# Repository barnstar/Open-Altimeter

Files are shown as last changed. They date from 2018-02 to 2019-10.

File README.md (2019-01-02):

# OpenAltimeter

## Concept

This was originally a project to build a simple altimeter to record
the apogee of mid power rocket flights... Then things got out of hand
as they are liable to do in this hobby........

The complex version runs on  an ESP8266 (or compatible) and includes 
sensor fusion to calculate spatial orientation, pyro and servo channels,
a web server and an  oled display to provide a "nice" user interface.

The "simple" version is designed for an Arduino nano and has no
interface beyond the serial logger and the indicator LEDs.

## Hardware

To build this, you'll need an Arduino - a nano is best or an ESP8266.
An ESP12 should also work but hasn't been tested.

The pinouts are noted in Configuration.h.  There are several
LEDs for indicators, a pin for an active peizo and two pins which
can be used for firing ematches via an NPN mosfet.  Two pins are also
allocated to control servos for parachute deployment (and/or for active
flight control for the ambitious).

The complex version also includes support for Oled displays via i2c.
A second switch can be used to navigate between the screens.

Notes:
- Power can be supplied from a 2s lipo.  Both the arduino nano
  and ESP8266 based boards like the Node MCU v1.0 will happily run off
  of an ~7.4V supply.   If using a nano with only a barometer, you
  can also use a pair of lithium button cells to construct a unit not 
  much larger than a a commercial altimeter.
- For deployment, it is advised to add a ~1A 5V regulator to drive
  the servos and/or mosfets.  You can get away with powering a small
  piezo and the indicator LEDs directly from the logic pin but be
  cautious.  Use a transistor switch for anything that exceeds the 
  single pin current rating for whichever micro controller you choose.
  You may be able to drive a small servo from the arduino 5V Vout as
  well.  This will not work for any board with 3.3V logic.

...Happy Flying

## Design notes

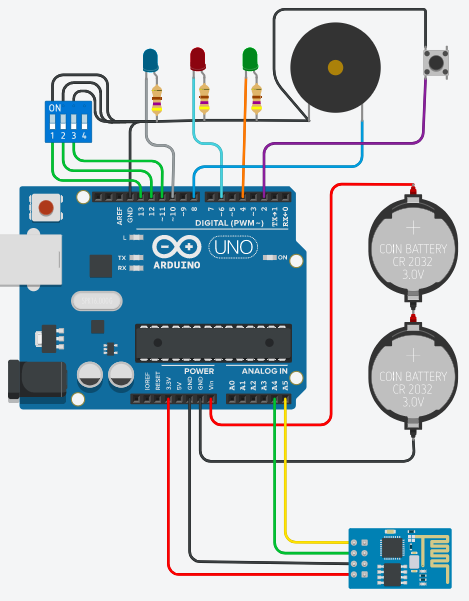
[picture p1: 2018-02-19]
Schematic.png

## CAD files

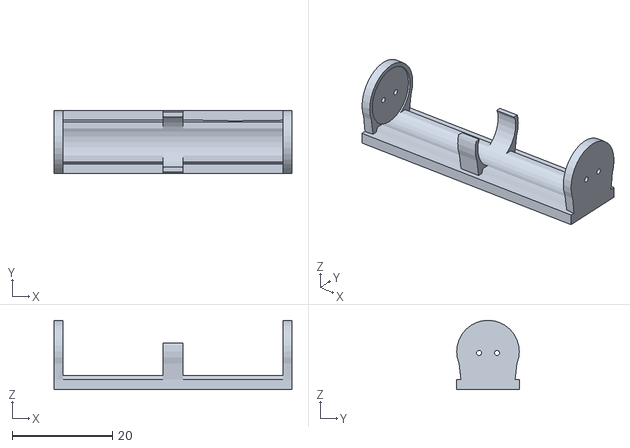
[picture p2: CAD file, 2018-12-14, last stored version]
Mechanical Parts/AAA-single.stl
47.5 x 12.5 x 13.9

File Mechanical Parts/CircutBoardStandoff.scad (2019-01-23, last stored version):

// Prototype board standoffs
//
//  by Jonathan Nobels, 2019
//
//  I dedicate any and all copyright interest in this software to the public domain.
//  I make this dedication for the benefit of the public at large and to the
//  detriment of my heirs and successors. I intend this dedication to be an overt
//  act of relinquishment in perpetuity of all present and future rights to this
//  software under copyright law. See <http://unlicense.org> for more info.
//

//Large Proto Board
SO_W=46;
SO_L=66;

//Small Proto Board
//SO_W=16;
//SO_L=76;

//4 Relay Board
//SO_W=48;
//SO_L=69;

W = SO_W+8;
L = SO_L+8;
H = 2;

SO_OD = 7;
SO_ID = 2.4;
SO_H = 10;
CO_RATIO = .66;

$fn=60;

base();

translate([-SO_W/2, -SO_L/2,0]) 
standoff();

translate([SO_W/2, -SO_L/2,0]) 
standoff();

translate([-SO_W/2, SO_L/2,0]) 
standoff();

translate([SO_W/2, SO_L/2,0]) 
standoff();


module base() {
   {
    difference() {
      translate([-W/2, -L/2,0])
      cube([W,L,H]);
      cube([W*CO_RATIO,L*CO_RATIO,H*2],center=true);
    }
  }
}
  
module standoff()
{
  difference() {
   cylinder(r=SO_OD/2, h=SO_H); 
   cylinder(r=SO_ID/2, h=SO_H*2); 
  } 
}

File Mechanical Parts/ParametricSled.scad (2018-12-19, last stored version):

//Av bay inner tube diameter
AVBAY_ID = 66.6;

//Microcontroller standoff spacing
MC_SO_HSPACE = 12.5;
MC_SO_VSPACE = 22.5;

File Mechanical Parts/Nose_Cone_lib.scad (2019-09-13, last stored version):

// Parametric Nose Cones
// 2 or 3 piece with removable tip and sleeve
//
//  by Jonathan Nobels, 2017
//
//  I dedicate any and all copyright interest in this software to the public domain.
//  I make this dedication for the benefit of the public at large and to the
//  detriment of my heirs and successors. I intend this dedication to be an overt
//  act of relinquishment in perpetuity of all present and future rights to this
//  software under copyright law. See <http://unlicense.org> for more info.
//

//Cone styles
PARABOLIC = 1;
OGIVE = 2;
HAACK = 3;
ELLIPTICAL = 4;

STYLE = OGIVE;

$fn=50;

//Tube Sytles
TUBE_15MT = 0;   //1.5" Mailing Tube
TUBE_25MT = 1;   //2.5" Mailing Tube
TUBE_30MT = 2;   //3.0" Mailing Tube
TUBE_22TW = 3;   //2.2" Thick Wall (Rocketarium)
TUBE_25TW = 4;   //2.5" Thick Wall (Rocketaruim)
TUBE_BT80 = 5;   //Estes BT80 (2.5")
TUBE_BT60 = 6;   //Estes BT60
TUBE_BT50 = 7;   //Estes BT50
TUBE_BT55 = 8;   //Estes BT55

TUBE_TYPE = TUBE_22TW;


LENGTH  = 130;         //Overall length of nose cone
TIP_LEN = 20;         //Length of the removable tip
TIP_RAD = 2;          //Tip radius
SHOULDER_LENGTH = 67; //Length of the insert/avbay

//The radii and lengths here have to be customized for each length/od
//Deriving the raduis at a given z position is left as an exercise for
//the reader.
SLEEVE_OR = 22.5; //Tip insery sleeve outer radius
SLEEVE_IR = 11;   //Tip insert sleeve inner radius
SLEEVE_LEN = 15;  //Tip sleeve length

WALL_THICKNESS = 2.0; //Cone and sleeve wall thickness
TOL = 0.0;

SEGMENTS = 100;


DIAMETERS=[
    //1.5" Mailing Tube
    [38.2, 41.2],
    //2.5" Mailing Tube
    [63.65, 66.90],
    //3.0" Mailing Tube
    [75.75, 78.75],
    //Rocketarium thick wall 2.2" Tube
    //OD.: 2.26. I.D.: 2.14
    [2.14 * 25.4, 2.26 * 25.4],
    //Rocketarium thick wall 2.5" Tube
    //O.D.: 2.638. I.D.: 2.558
    [2.558 *25.4, 2.638 *25.4],
    //BT50 ID: 0.95", OD: 0.976"
    [0.95*25.4, 0.976*25.4],
    //BT60: ID: 1.595", OD: 1.637
    [1.595*25.4,1.637*25.4],
    //BT80: OD: 2.6" ID: 2.558"
    [2.558*25.4,  2.60*25.4],
    //BT55
    [32.6, 33.7]
];

TUBE_ID = DIAMETERS[TUBE_TYPE][0] - TOL;
TUBE_OD = DIAMETERS[TUBE_TYPE][1];


// Components
module bulkhead()
{
  difference()
  {
    union()
    {
      cylinder(r = TUBE_ID / 2, h = 3.5, center = false);
      cylinder(r = TUBE_ID / 2 - WALL_THICKNESS - .1, h = 6.0, center = false);
    }
    cylinder(r = 1.5, h = 20, center = true);
    for (x = [ -TUBE_ID / 2 + 8, TUBE_ID / 2 - 8 ])
    {
      translate([ x, 0, 0 ])
      {
        cylinder(r = 3.0, h = 20, center = true);
      }
    }
  }
}

module simple_insert_nobase()
{
  union()
  {
    difference()
    {
      union(){
      cylinder(r = TUBE_OD / 2 - WALL_THICKNESS, h = SHOULDER_LENGTH+10, center = false);
      cylinder(r = TUBE_ID / 2, h = SHOULDER_LENGTH, center = false);
      }
      translate([0,0,-3]) {
      cylinder(r = TUBE_ID / 2 - WALL_THICKNESS, h = (SHOULDER_LENGTH)*2.8, center = false);
      }
    }
  }
}

module simple_coupler()
{
  union()
  {
    difference()
    {
      union(){
      cylinder(r = TUBE_OD / 2 - WALL_THICKNESS, h = SHOULDER_LENGTH+10, center = false);
      cylinder(r = TUBE_ID / 2, h = SHOULDER_LENGTH, center = false);
      }
      translate([0,0,-3]) {
      cylinder(r = TUBE_ID / 2 - WALL_THICKNESS, h = (SHOULDER_LENGTH)*2.8, center = false);
      }
    }
  }
}

module simple_insert()
{
  union()
  {
    difference()
    {
      union(){
      //cylinder(r = TUBE_OD / 2 - WALL_THICKNESS, h = SHOULDER_LENGTH+10, center = false);
      cylinder(r = TUBE_ID / 2, h = SHOULDER_LENGTH, center = false);
      }
      translate([0,0,3]) {
      cylinder(r = TUBE_ID / 2 - WALL_THICKNESS, h = (SHOULDER_LENGTH)*2.8, center = false);
      }
    }
  }
}

module avbay_insert()
{
  union()
  {
    difference()
    {
      cylinder(r = TUBE_ID / 2, h = SHOULDER_LENGTH, center = false);
      cylinder(r = TUBE_ID / 2 - WALL_THICKNESS, h = (SHOULDER_LENGTH)*2.1, center = true);
    }
    difference()
    {
      union()
      {
        translate([ TUBE_ID / 2 - WALL_THICKNESS - 11, -5, 3.5 ])
        {
          cube([ 12, 10, 14 ]);
        }
        translate([ -TUBE_ID / 2 + WALL_THICKNESS - 1, -5, 3.5 ])
        {
          cube([ 12, 10, 14 ]);
        }
      }
      for (x = [ -TUBE_ID / 2 + 8, TUBE_ID / 2 - 8 ])
      {
        translate([ x, 0, 0 ])
        {
          cylinder(r = 3.0, h = 70, center = true);
        }
      }
    }
  }
}

module avbay_retainer()
{
  or = TUBE_ID / 2 - WALL_THICKNESS - .75;
  ir = or *.45;

  difference()
  {
    union()
    {
      translate([ 0, 0, 10 ])
      {
        cube([ or * 1.9, 9, 20 ], center = true);
      }
      cylinder(h = 3, r = or, center = false);
    }
    rotate([ 0, 0, 90 ]) translate([ TUBE_ID / 2 - WALL_THICKNESS - 12, -5.5, -1 ])
    {
      cube([ 12.8, 11, 24 ]);
    }
    rotate([ 0, 0, 90 ]) translate([ -TUBE_ID / 2 + WALL_THICKNESS - 1, -5.5, -1 ])
    {
      cube([ 12.8, 11, 24 ]);
    }
    translate([ 0, 0, -1 ])
    {
      //cylinder(h=50, r=ir, center=true);
      cube(size = [ 20, 20, 40 ], center = true);
    }
    translate([ 0, 0, 17 ])
        cube([ 51, 2.2, 25 ], center = true);
    translate([ 0, 0, 23 ])
        cube([ 46, 40, 28 ], center = true);
  }
}

module solid_cone()
{
  if (STYLE == ELLIPTICAL)
  {
    cone_elliptical(R = TUBE_OD / 2, L = LENGTH, s = SEGMENTS);
  }
  if (STYLE == OGIVE)
  {
    cone_ogive_tan_blunted(R = TUBE_OD / 2, R_nose = TIP_RAD, L = LENGTH, s = SEGMENTS);
  }
  if (STYLE == PARABOLIC)
  {
    cone_parabolic(R = TUBE_OD / 2, L = LENGTH, s = SEGMENTS);
  }
  if (STYLE == HAACK)
  {
    cone_haack(R = TUBE_OD / 2, L = LENGTH, s = SEGMENTS, R_nose = TIP_RAD);
  }
}

module shelled_cone()
{
  difference()
  {
    if (STYLE == ELLIPTICAL)
    {
      difference()
      {
        cone_elliptical(R = TUBE_OD / 2, L = LENGTH, s = SEGMENTS);
        cone_elliptical(R = TUBE_OD / 2 - WALL_THICKNESS, L = LENGTH - WALL_THICKNESS, s = SEGMENTS);
      }
    }
    if (STYLE == OGIVE)
    {
      difference()
      {
        cone_ogive_tan_blunted(R = TUBE_OD / 2, R_nose = TIP_RAD, L = LENGTH, s = SEGMENTS);
        cone_ogive_tan_blunted(R = TUBE_OD / 2 - WALL_THICKNESS, R_nose = TIP_RAD, L = LENGTH * .96, s = SEGMENTS);
      }
    }
    if (STYLE == PARABOLIC)
    {
      difference()
      {
        cone_parabolic(R = TUBE_OD / 2, L = LENGTH, s = SEGMENTS);
        cone_parabolic(R = TUBE_OD / 2 - WALL_THICKNESS, L = LENGTH - WALL_THICKNESS, s = SEGMENTS);
      }
    }
    if (STYLE == HAACK)
    {
      difference()
      {
        cone_haack(R = TUBE_OD / 2, L = LENGTH, s = SEGMENTS, R_nose = TIP_RAD);
        cone_haack(R = TUBE_OD / 2 - WALL_THICKNESS, L = LENGTH - WALL_THICKNESS, s = SEGMENTS);
      }
    }
    //Cut out inner sleeve
    //cylinder(r = TUBE_ID / 2, h = 20, center = true);
  }
  //The tip support tends to detach during printing.  This bar is removable and 
  //will prevent that
  //translate([0,0,1])
  //cube([TUBE_OD-WALL_THICKNESS/2,5,2], center=true);
}

module cone_bottom()
{
  difference()
  {
    union()
    {
      shelled_cone();
      translate([ 0, 0, LENGTH - TIP_LEN - SLEEVE_LEN ]) difference()
      {
        cylinder(r = SLEEVE_OR, h = SLEEVE_LEN * 2, center = false);
        cylinder(r = SLEEVE_IR, h = SLEEVE_LEN * 4, center = true);
      }
    }
    translate([ -SLEEVE_OR * 2.5, -SLEEVE_OR * 2.5, LENGTH - TIP_LEN ]) cube([ SLEEVE_OR * 5, SLEEVE_OR * 5, TIP_LEN * 2 ]);
  }
}

module cone_tip()
{
  translate([ 0, 0, -(LENGTH - TIP_LEN - SLEEVE_LEN) ])
  {
    union()
    {
      difference()
      {
        solid_cone();
        translate([ -TUBE_OD, -TUBE_OD, 0 ]) cube([ TUBE_OD * 2, TUBE_OD * 2, LENGTH - TIP_LEN ]);
      }
      translate([ 0, 0, LENGTH - TIP_LEN - SLEEVE_LEN ])
          cylinder(r = SLEEVE_IR - .4, h = SLEEVE_LEN, center = false);
    }
  }
}

module cone_haack(C = 0, R = 5, L = 10, s = 100)
{
  // SEARS-HAACK BODY NOSE CONE:
  //
  // Parameters:
  // C = 1/3: LV-Haack (minimizes supersonic drag for a given L & V)
  // C = 0: LD-Haack (minimizes supersonic drag for a given L & D), also referred to as Von Kármán
  //
  // Formulae (radians):
  // theta = acos(1 - (2 * x / L));
  // y = (R / sqrt(PI)) * sqrt(theta - (sin(2 * theta) / 2) + C * pow(sin(theta),3));

  echo(str("SEARS-HAACK BODY NOSE CONE"));
  echo(str("C = ", C));
  echo(str("R = ", R));
  echo(str("L = ", L));
  echo(str("s = ", s));

  TORAD = PI / 180;
  TODEG = 180 / PI;

  inc = 1 / s;

  rotate_extrude(convexity = 10, $fn = s) for (i = [1:s])
  {
    x_last = L * (i - 1) * inc;
    x = L * i * inc;

    theta_last = TORAD * acos((1 - (2 * x_last / L)));
    y_last = (R / sqrt(PI)) * sqrt(theta_last - (sin(TODEG * (2 * theta_last)) / 2) + C * pow(sin(TODEG * theta_last), 3));

    theta = TORAD * acos(1 - (2 * x / L));
    y = (R / sqrt(PI)) * sqrt(theta - (sin(TODEG * (2 * theta)) / 2) + C * pow(sin(TODEG * theta), 3));
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

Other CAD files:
Mechanical Parts/RocketComponentLib.scad
Mechanical Parts/U_Box_V103.scad
Mechanical Parts/threads.scad

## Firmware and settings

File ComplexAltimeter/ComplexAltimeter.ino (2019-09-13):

/*********************************************************************************
 * Open Altimeter
 *
 * Mid power rocket avionics software for altitude recording and dual deployment
 *
 * Copyright 2018, Jonathan Nobels
 *
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
 * THE SOFTWARE IS PROVIDED "AS IS", WITHOUT WARRANTY OF ANY KIND, EXPRESS OR
 * IMPLIED, INCLUDING BUT NOT LIMITED TO THE WARRANTIES OF MERCHANTABILITY,
 * FITNESS FOR A PARTICULAR PURPOSE AND NONINFRINGEMENT. IN NO EVENT SHALL THE
 * AUTHORS OR COPYRIGHT HOLDERS BE LIABLE FOR ANY CLAIM, DAMAGES OR OTHER
 * LIABILITY, WHETHER IN AN ACTION OF CONTRACT, TORT OR OTHERWISE, ARISING FROM,
 * OUT OF OR IN CONNECTION WITH THE SOFTWARE OR THE USE OR OTHER DEALINGS IN THE
 * SOFTWARE.
 **********************************************************************************/

#define VERSION 1

#include "src/FlightController.hpp"
#include "src/Sensor/I2CUtil.h"

void setup()
{
 Serial.begin(57600);

  //Scan the i2c bus for debugging
  scanI2cBus();
  
  //Initialize the shared flightController
  FlightController::shared();
}

void loop()
{
  FlightController::shared().loop();
}

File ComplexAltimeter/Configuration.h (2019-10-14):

/*********************************************************************************
 * Open Altimeter
 *
 * Mid power rocket avionics software for altitude recording and dual deployment
 *
 * Copyright 2018, Jonathan Nobels
 *
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
 * THE SOFTWARE IS PROVIDED "AS IS", WITHOUT WARRANTY OF ANY KIND, EXPRESS OR
 * IMPLIED, INCLUDING BUT NOT LIMITED TO THE WARRANTIES OF MERCHANTABILITY,
 * FITNESS FOR A PARTICULAR PURPOSE AND NONINFRINGEMENT. IN NO EVENT SHALL THE
 * AUTHORS OR COPYRIGHT HOLDERS BE LIABLE FOR ANY CLAIM, DAMAGES OR OTHER
 * LIABILITY, WHETHER IN AN ACTION OF CONTRACT, TORT OR OTHERWISE, ARISING FROM,
 * OUT OF OR IN CONNECTION WITH THE SOFTWARE OR THE USE OR OTHER DEALINGS IN THE
 * SOFTWARE.
 **********************************************************************************/

#ifndef config_h
#define config_h

#include <Arduino.h>
#include "src/types.h"

// There are two cheap types of OLED displays.  Choose the one that doesn't
// output gargabe.  I2C ony supported here.  #define the one you're using.
#define USE_SH1106
//#define USE_SDD1306

// Display width and height for the SDD1306 constructor
#define kDispWidth 128
#define kDispHeight 64

// Set this to 0 to disable the display while in flight
#define RUN_DISPLAY_WHILE_FLYING 0

// Recording will start at FLIGHT_START_THRESHOLD_ALT m and we'll assume we're
// on the ground at FLIGHT_END_THRESHOLD_ALT m. In theory, these could be lower,
// but we want to account for landing in a tree, on a hill, etc.  30m should be
// sufficient for most launch sites.
const double FLIGHT_START_THRESHOLD_ALT      = 10;
const double FLIGHT_END_THRESHOLD_ALT        = 30;
const double FLIGHT_START_THRESHOLD_ACC      = 20.0;  // in mss
const double FLIGHT_START_THRESHOLD_VELOCITY = 0.5;  // m/s
const double FLIGHT_END_THRESHOLD_VELOCITY   = 0.0;  // m/s
const float FAILSAFE_ALTITUDE                = -10; 

// When the altitude is DESCENT_THRESHOLD meters less than the apogee, we'll
// assume we're descending.  Hopefully, your rocket has a generally upwards
// trajectory....
const double DESCENT_THRESHOLD = 15;

// Maximum on time for pyro type deployment
const int MAX_FIRE_TIME = 5000;

// ESP8266 specific
#define SD2 9
#define SD3 10

#define ENABLE_GIMBALLING 1

// D1 & D2 are used for i2c
const int SERIAL_BAUD_RATE = 57600;

#define CONFIG2
//#define CONFIG1  

#ifdef CONFIG1
const byte STATUS_PIN      = NO_PIN;  // Unit status pin.  On if OK
const byte MESSAGE_PIN     = D6;      // Blinks out the altitude
const byte READY_PIN       = D5;      // Indicates the unit is ready for flight
const byte BUZZER_PIN      = D0;      // Audible buzzer on landing
const byte RESET_PIN       = SD2;     // SD2 - pin "9"
const byte INPUT_PIN       = SD3;     // SD3 - pin "10"

#if !ENABLE_GIMBALLING
const byte DEPL_CTL_1           = D3;  // control pin 1
const byte DEPL_CTL_2           = D4;  // control pin 2
const byte PITCH_CONTROL_PIN     = NO_PIN;
const byte YAW_CONTROL_PIN       = NO_PIN;
#else
const byte DEPL_CTL_1           = NO_PIN;  // control pin 1
const byte DEPL_CTL_2           = NO_PIN;  // control pin 2
const byte PITCH_CONTROL_PIN     = D3;
const byte YAW_CONTROL_PIN       = D4;
#endif

const byte DEPL_CTL_3           = D7;  // control pin 1
const byte DEPL_CTL_4           = D8;  // control pin 2
const RecoveryDeviceType CTL_1_TYPE = kServo;  //PWM control
const RecoveryDeviceType CTL_2_TYPE = kServo;  //PWM control 
const RecoveryDeviceType CTL_3_TYPE = kPyro;   //On/off
const RecoveryDeviceType CTL_4_TYPE = kPyro;   //On/off
const int BARO_I2C_ADDR     = 0x76;  // 0x77 or 0x76
const int DISPLAY_I2C_ADDR  = 0x3C;
const int IMU_I2C_ADDR      = 0x68;
const PeizoStyle PEIZO_TYPE = kActive;
#define USE_BMP085 1
#define USE_MPU9250 1
#endif



#ifdef CONFIG2
const byte STATUS_PIN      = NO_PIN;  // Unit status pin.  On if OK
const byte MESSAGE_PIN     = NO_PIN;      // Blinks out the altitude
const byte READY_PIN       = NO_PIN;      // Indicates the unit is ready for flight
const byte BUZZER_PIN      = D0;      // Audible buzzer on landing
const byte RESET_PIN       = NO_PIN;     // SD2 - pin "9"
const byte INPUT_PIN       = NO_PIN;     // SD3 - pin "10"
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

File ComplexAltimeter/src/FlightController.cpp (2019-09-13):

/*********************************************************************************
 * Open Altimeter
 *
 * Mid power rocket avionics software for altitude recording and dual deployment
 *
 * Copyright 2018, Jonathan Nobels
 *
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
 * THE SOFTWARE IS PROVIDED "AS IS", WITHOUT WARRANTY OF ANY KIND, EXPRESS OR
 * IMPLIED, INCLUDING BUT NOT LIMITED TO THE WARRANTIES OF MERCHANTABILITY,
 * FITNESS FOR A PARTICULAR PURPOSE AND NONINFRINGEMENT. IN NO EVENT SHALL THE
 * AUTHORS OR COPYRIGHT HOLDERS BE LIABLE FOR ANY CLAIM, DAMAGES OR OTHER
 * LIABILITY, WHETHER IN AN ACTION OF CONTRACT, TORT OR OTHERWISE, ARISING FROM,
 * OUT OF OR IN CONNECTION WITH THE SOFTWARE OR THE USE OR OTHER DEALINGS IN THE
 * SOFTWARE.
 **********************************************************************************/

#include "FlightController.hpp"
#include <FS.h>
#include "DataLogger.hpp"

#include "../Configuration.h"
#include "types.h"

#define kMaxBlinks 64

FlightController::FlightController() : imu(1000 / SENSOR_READ_DELAY_MS)
{
  SPIFFS.begin();

  Serial.begin(SERIAL_BAUD_RATE);
  DataLogger::sharedLogger();

  DataLogger::log("Creating Flight Controller");
  blinker = new Blinker(MESSAGE_PIN, BUZZER_PIN);
  DataLogger::log("Creating Flight Controller --");

  this->initialize();
  DataLogger::log("Flight Controller Initialized");

  bool success = false;
  int deplAlt  = settings.readIntValue(F("DepAlt"), &success);
  if (success) {
    DataLogger::log("Read Deployment Altitude");
    deploymentAltitude = deplAlt;
  } else {
    DataLogger::log("Set default deployment altitude 100");
    settings.writeIntValue(100, F("DepAlt"));
  }
}

FlightController::~FlightController() { delete blinker; }

FlightController &FlightController::shared()
{
  static FlightController sharedInstance;
  return sharedInstance;
}

void FlightController::initialize()
{
  DataLogger::log("Initializing Flight Controller");

  IPAddress serverAddress(IPAddress(192, 4, 0, 1));
  server.start(serverAddress);

  pinMode(RESET_PIN, INPUT_PULLUP);

  // All LED pins sset to outputs
  pinMode(MESSAGE_PIN, OUTPUT);
  pinMode(STATUS_PIN, OUTPUT);
  pinMode(READY_PIN, OUTPUT);
  pinMode(BUZZER_PIN, OUTPUT);

  // Start in the "error" state.  Status pin should be high and message
  // pin should be low to indicate a good startup
  digitalWrite(STATUS_PIN, LOW);
  digitalWrite(MESSAGE_PIN, HIGH);

  barometerReady = altimeter.start();
  mpuReady       = imu.start();

  flightData.reset();

  DataLogger::log("Deployment Altitude: " + String(deploymentAltitude));
  DataLogger::log("Pressure:" + String(altimeter.getRefPressure()));
  // We don't want to sound the buzzer on first boot, only after a flight
  enableBuzzer = false;
}

void FlightController::initRecoveryDevices()
{
  bool didRead = false;
  int onAngle  = settings.readIntValue("servoOnAngle", &didRead);
  if (!didRead) {
    onAngle = kChuteReleaseTriggeredAngle;
  }

  didRead      = false;
  int offAngle = settings.readIntValue("servoOffAngle", &didRead);
  if (!didRead) {
    offAngle = kChuteReleaseArmedAngle;
  }

  for (int i = 0; i < 4; i++) {
    devices[i] = new RecoveryDevice();
  }

  RecoveryDevice::setOffAngle(offAngle, false);
  RecoveryDevice::setOnAngle(onAngle, false);

#if !ENABLE_GIMBALLING
  devices[0]->init(ControlChannel1, DEPL_CTL_1, CTL_1_TYPE);
  devices[1]->init(ControlChannel2, DEPL_CTL_2, CTL_2_TYPE);
  setMainChannel(ControlChannel1);
  setDrogueChannel(ControlChannel2);
#else
  //Use pyro channels gimballing
  devices[2]->init(ControlChannel3, DEPL_CTL_3, CTL_3_TYPE);
  devices[3]->init(ControlChannel4, DEPL_CTL_4, CTL_4_TYPE);
  setMainChannel(ControlChannel3);
  setDrogueChannel(ControlChannel4);

  attitudeControl = new AttitudeControl(imu);
#endif
}

void FlightController::setMainChannel(int channel)
{
  mainChute = getRecoveryDevice(channel);
}

void FlightController::setDrogueChannel(int channel)
{
  drogueChute = getRecoveryDevice(channel);
}

RecoveryDevice *FlightController::getRecoveryDevice(int channel)
{
  // Array location is 0 indexed... Channels are 1 indexed.
  return devices[channel - 1];
}

StatusData const &FlightController::getStatusData()
{
  statusData.deploymentAlt     = deploymentAltitude;
  statusData.status            = flightState;
  statusData.baroReady         = barometerReady;
  statusData.mpuReady          = mpuReady;
  statusData.padAltitude       = altimeter.referenceAltitude();
  statusData.lastApogee        = flightData.apogee;
  statusData.referencePressure = altimeter.getRefPressure();

  return statusData;
}

String FlightController::getStatus()
{
  String statusStr =
      (flightState == kReadyToFly ? F("Ready To Fly") : F("Waiting"));

  String ret;
  ret += "Status :" + statusStr + "<br/>";
  ret += "Flight Count :" + String(flightCount) + "<br/>";
  ret += "Deployment Altitude: " + String(deploymentAltitude) + "<br/>";
  ret += "Pad Altitude:" + String(altimeter.referenceAltitude()) + "<br/>";
  if (flightState != kReadyToFly) {
    ret += "Last Flight:" + flightData.toString(flightCount) + "<br/>";
  }
  return ret;
}

void readSensors(FlightController *f)
{
  if (f != nullptr) {
    f->sampleOnNextLoop = true;
  }
}

void FlightController::loop()
{
  if (!interfaceStarted) {
    interfaceStarted = true;
    initRecoveryDevices();
    userInterface.start();
  }
  failsafeCheck();


  // Ignore the wifis and oled when we're flying.
  if (flightState == kReadyToFly || flightState == kOnGround) {
    server.handleClient();
    userInterface.eventLoop(true);
  } else {
    userInterface.eventLoop(false);
  }

  if (sampleOnNextLoop) {
    flightControl();
    attitudeControl->update();
    sampleOnNextLoop = false;
  }

  if (flightState == kReadyToFly && altimeter.isReady() &&
      !sensorTicker.active())
  {
    DataLogger::log(F("Starting Ticker"));
    blinker->cancelSequence();
    blinker->blinkValue(2, 300, true, false);
    DataLogger::sharedLogger().openFlightDataFileWithIndex(flightCount);
    sensorTicker.attach_ms(SENSOR_READ_DELAY_MS, readSensors, this);
    digitalWrite(READY_PIN, HIGH);
    flightControl();
  }

  if (flightState == kAscending && blinker->isBlinking()) {
    blinker->cancelSequence();
  }

  // Blink out the last recorded apogee on the message pin
  if (flightState == kOnGround && sensorTicker.active()) {
    DataLogger::log(F("Stopping Ticker"));
    sensorTicker.detach();
    flightControl();
    blinker->cancelSequence();
    digitalWrite(READY_PIN, LOW);
    if (lastApogee) {
      DataLogger::log(String(F("Starting Blinker: ")) + String(lastApogee));
      blinker->blinkValue(lastApogee, BLINK_SPEED_MS, true);
      lastApogee = 0;
    }
  }
}
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

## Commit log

2018-02-03 Added support for a second deployment relay triggered at apogee for proper dual deployment. Added support for the cheaper BMP280 clones.
2018-02-19 Updates to some logic and pinouts
    Added usage instructions and a schematic
2018-04-14 All compilation issues fixed. /stats working / working All flights getting logged to a JSON flat file instead of EEPROM
    [ComplexAltimeter.ino, DataLogger.cpp, FlightController.cpp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]
2018-04-14 Added Logging of flight data points /resetAll /reset /flights /flight/<x>
    [Altimeter.cpp, ComplexAltimeter.ino, DataLogger.cpp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]
2018-04-16 Preliminary IMU support
2018-08-26 Added Kalman filters to both the simple and complex variants for the pressure/ altitude.
    Updated some logic in the simple alitimeter
    for better fail-safety.
    [Altimeter.cpp, FlightController.cpp, SimpleAltimeter.ino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]
2018-11-09 Refactored SimpleAltimeter into separate classes
    Added an interrupt based blink output
    Added BMP085 support
2018-11-09 Adding new files
    [Configuration.h]
2018-11-10 Syntax Errors and Compilation Fixes
    Added SimpleTimer
    [Configuration.h]
2018-11-13 Memory Optimization Adding sensor fusion lib
    [Configuration.h]
2018-11-15 Refactoring the timer to take an abstract class in lieu of function pointers.
    Adding a ButtonInput class.
2018-11-15 Adding delegate support to ButtonInput in addition to raw function pointers.
2018-11-15 Blinker Bug Fixes Added sensor fusion to read roll/pitch/yaw
    [Configuration.h]
2018-11-15 Timer interrupt syntax fixes. Runs.
    [SimpleAltimeter.ino]
2018-11-17 Lots of compilation fixes for ComplexAltimeter. Untested, but it'll build.
    [Altimeter.cpp, FlightController.cpp]
2018-11-18 Switched to SFE BMP lib. Lots of little bug fixes. ComplexAltimeter runs on an ESP8266 SimpleAltimeter runs on a Nano
    [Altimeter.cpp, DataLogger.cpp, FlightController.cpp]
2018-11-20 More reformatting
    [Configuration.h]
2018-11-20 Even more formatting
    [Configuration.h]
2018-11-22 Adding license headers. Spelling corrections. File reorganizaion. Some skeleton header work for OLED display
    [Configuration.h]
2018-11-23 Preliminary OLED Display Support Not Working
    [DisplayIface.h, FlightController.cpp]
2018-11-28 VS Code Arduino Setup Working through the mess of syntax errors
    [Altimeter.cpp, DisplayIface.h, FlightController.cpp]
2018-11-28 Removing unnecessary bundled libs Adding all required dependencies to the project tree though this has the effect of breaking things if you have these libs installed via the Arduino lib manager - it 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
    Project should now compile. Display support still untested.
2018-12-14 Removed duplicate files and replaced with SymLinks
    [AAA-single.stl, Configuration.h, U_Box_V103.scad]
2018-12-14 Correcting errors in Complex
    [RecoveryDevice.cpp]
2018-12-19 Cleanup. Added header for simple.
    [Configuration.h, ParametricSled.scad]
2018-12-30 Adding mechanical parts. Configuration Cleanup
    [AAA-single.stl, Configuration.h, Nose_Cone_lib.scad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]
2019-01-01 Added SH1106 Oled Support DataLogger Bug Fixes
    [Configuration.h, Nose_Cone_lib.scad, RocketComponentLib.scad]
2019-01-02 Blinker class now common Added acc and gyro display General sensor related code cleanup
2019-01-03 UI Refactor
    [Configuration.h]
2019-01-04 Creating a filter package Experimenting with velocity from altitude Fixing some issues with disp refresh
    [Configuration.h]
2019-01-07 Added test page Updated HTML interface
    [Configuration.h]
2019-01-08 HTML Updates and some fixes to TestView Servos not working
    [Configuration.h]
2019-01-08 Refactoring, renaming. Possible servo fix.
    [Configuration.h]
2019-01-10 Web UI Sensor Work
    [Configuration.h]
2019-01-12 Optimizing for sample rate
    [Configuration.h]
2019-01-15 Cleanup and optimizations
    [RocketComponentLib.scad]
2019-01-22 Servo fix.
    [CircutBoardStandoff.scad, Configuration.h, Nose_Cone_lib.scad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]
2019-01-23 SCAD file cleanup General formatting
    [CircutBoardStandoff.scad, Configuration.h, Nose_Cone_lib.scad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]
2019-02-11 Experimental failsafe check
    [Configuration.h]
2019-02-23 Correcting errors in components
    [Nose_Cone_lib.scad, RocketComponentLib.scad]
2019-08-01 Added very basic and completely untested attitude control
    Added the required sensor libraries directly.
    [Configuration.h]
2019-09-12 Added 24 to 29mm adapter rings Added (totally untested) feedback to the attitude control logic.
    [RocketComponentLib.scad]
2019-09-13 Component Lib Fixes
    [Configuration.h, Nose_Cone_lib.scad, RocketComponentLib.scad]
2019-10-14 New configuration
    [Configuration.h, RocketComponentLib.scad]
2019-10-15 Config changes.
    Failsafe tested and working. Added a cancel
    function so a second reset press while flying
    will reset the unit. Tweaks to the logic for
    selecting altitudes.
    Nested if's instead of && for clarity.
    [Configuration.h]
